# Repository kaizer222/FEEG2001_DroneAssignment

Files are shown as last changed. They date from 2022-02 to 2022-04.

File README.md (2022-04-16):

# FEEG2001_DroneAssignment
GROUP 11 FEEG2001 SEMESTER 2 MULTIROTOR DESIGN PROJECT 

Arduino Code is now tested and working! 

Contribution:
1) SD Card coding	:	James Tang
2) MPU coding		:	Kai Sheng
3) Gimbal coding	:	Kai Wen, Jayce
4) Troubleshooting	:	Kai Wen

To do:
1) Yaw axis stabilisation (optional)

Sources:
1) Gimbal Code	: https://howtomechatronics.com/projects/diy-arduino-gimbal-self-stabilizing-platform/
2) MPU Code	: https://github.com/ElectronicCats/mpu6050/tree/master/examples/MPU6050_DMP6

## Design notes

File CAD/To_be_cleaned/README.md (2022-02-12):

# SolidWorks 3D CAD Files  

## 🚀 Current development  
- Cuboid body with X-configuration arm
- Selection of landing gear
- Selection of material (FEA & Granta Edupack etc.) 

## 🧐 Changelog  
13 Feb 21 — Add files via upload  

## 📃 File extensions  
**`.SLDPRT`** &emsp; SOLIDWORKS Part File  
**`.SLDASM`** &emsp; SOLIDWORKS Assembly File  
**`.STL   `** &emsp;  File type compatible for 3D additive manufacturing  

*I'm using SOLIDWORKS 2020 Student Edition, so if you are using a more recent version it should be backwards compatible.*  

## ⚙ Contents  

### `Assembly1.SLDASM` 
 
<table>
  <tr align="center">
    <th>Component filename</th>
    <th>Description</th>
    <th>Quantity</th>
  </tr>
  <tr align="center">
    <td>arm.SLDPRT</td>
    <td>X-configuration arm</td>
    <td>1</td>
  </tr>
  <tr align="center">
    <td>blade.SLDPRT</td>
    <td>Rotor blade</td>
    <td>4</td>
  </tr>
  <tr align="center">
    <td>body.SLDPRT</td>
    <td>Hexagonal body</td>
    <td>1</td>
  </tr>
  <tr align="center">
    <td>gimbal1.SLDPRT</td>
    <td>Gimbal subpart</td>
    <td>1</td>
  </tr>
    <tr align="center">
    <td>gimbal2.SLDPRT</td>
    <td>Gimbal subpart</td>
    <td>1</td>
  </tr>
    <tr align="center">
    <td>gimbal3.SLDPRT</td>
    <td>Gimbal subpart</td>
    <td>1</td>
  </tr>
    <tr align="center">
    <td>gimbal4.SLDPRT</td>
    <td>Gimbal subpart</td>
    <td>1</td>
  </tr>
    <tr align="center">
    <td>camera.SLDPRT</td>
    <td>Camera</td>
    <td>1</td>
  </tr>
</table>

Associated .STL file: [concept1.STL](https://github.com/kaizer222/FEEG2001_DroneAssignment/blob/main/SolidWorks%20CAD/concept1.STL)  
*The gimbal model used in this assembly is inaccurate and oversimplified, please refer to `ggimbal_assem.SLDASM` instead.*

### `Assembly2.SLDASM` 
 
<table>
  <tr align="center">
    <th>Component filename</th>
    <th>Description</th>
    <th>Quantity</th>
  </tr>
  <tr align="center">
    <td>arm2.SLDPRT</td>
    <td>H-configuration arm</td>
    <td>1</td>
  </tr>
  <tr align="center">
    <td>blade.SLDPRT</td>
    <td>Rotor blade</td>
    <td>4</td>
  </tr>
  <tr align="center">
    <td>body2.SLDPRT</td>
    <td>Cuboid body</td>
    <td>1</td>
  </tr>
  <tr align="center">
    <td>angle_bracket_15x15x10.SLDPRT</td>
    <td>Angle bracket</td>
    <td>2</td>
</table>

Associated .STL file: [concept2.STL](https://github.com/kaizer222/FEEG2001_DroneAssignment/blob/main/SolidWorks%20CAD/concept2.STL)  

### `servo_assem.SLDASM`  

<table>
  <tr align="center">
    <th>Component filename</th>
    <th>Description</th>
    <th>Quantity</th>
  </tr>
  <tr align="center">
    <td>servo_body.SLDPRT</td>
    <td>Servo body</td>
    <td>1</td>
  </tr>
  <tr align="center">
    <td>servo_blade.SLDPRT</td>
    <td>Servo blade</td>
    <td>1</td>
  </tr>
</table>

Associated .STL file: [servo.STL](https://github.com/kaizer222/FEEG2001_DroneAssignment/blob/main/SolidWorks%20CAD/servo.STL)  
*The modelling of the servo itself is not important, but it helps when modelling the servo housing for the gimbal as in `ggimbal_assem.SLDASM`.*  

### `ggimbal_assem.SLDASM`  

<table>
  <tr align="center">
    <th>Component filename</th>
    <th>Description</th>
    <th>Quantity</th>
  </tr>
  <tr align="center">
    <td>servo_body.SLDPRT</td>
    <td>Servo body</td>
    <td>3</td>
  </tr>
  <tr align="center">
    <td>servo_blade.SLDPRT</td>
    <td>Servo blade</td>
    <td>3</td>
  <tr align="center">
    <td>camera_scaled.SLDPRT</td>
    <td>Just a fancier camera 📸</td>
    <td>1</td>
  </tr>
  <tr align="center">
    <td>servo_bolt.SLDPRT</td>
    <td>Servo bolt (short)</td>
    <td>2</td>
  </tr>
  <tr align="center">
    <td>servo_bolt_long.SLDPRT</td>
    <td>Servo bolt (long)</td>
    <td>4</td>
  </tr>
  <tr align="center">
    <td>servo_nut.SLDPRT</td>
    <td>Servo nut</td>
    <td>6</td>
  </tr>
  <tr align="center">
    <td>servo_housing1.SLDPRT</td>
    <td>Servo housing (roll direction)</td>
    <td>1</td>
  </tr>
  <tr align="center">
    <td>servo_housing2.SLDPRT</td>
    <td>Servo housing (pitch direction)</td>
    <td>1</td>
  </tr>
</table>

Associated .STL file: [gimbal.STL](https://github.com/kaizer222/FEEG2001_DroneAssignment/blob/main/SolidWorks%20CAD/gimbal.STL)  
*Three degrees of rotation freedom (DOF-3R), each with π radians.*

---

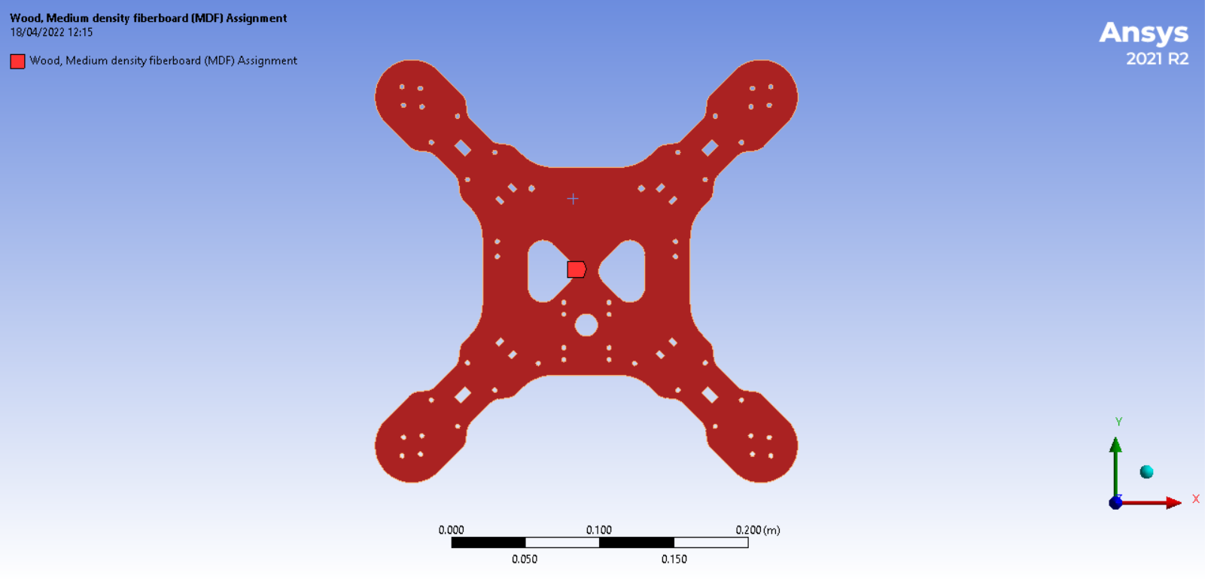
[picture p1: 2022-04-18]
img/Screenshot 2022-04-18 121616.png

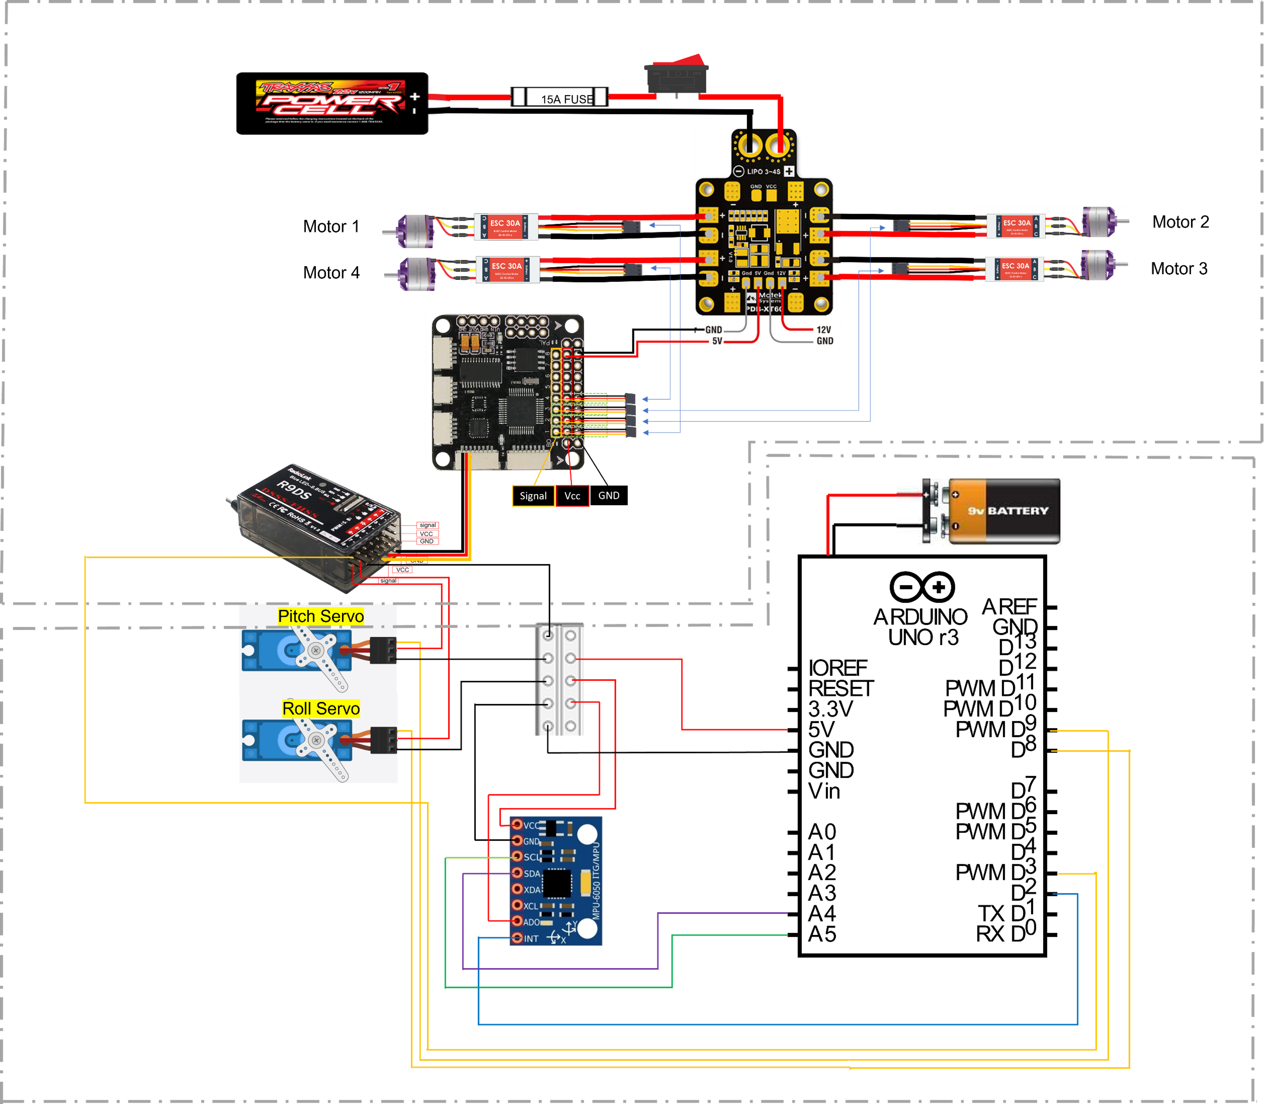
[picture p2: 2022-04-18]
circuit_diagram/pictorial_circuit_diagram.png

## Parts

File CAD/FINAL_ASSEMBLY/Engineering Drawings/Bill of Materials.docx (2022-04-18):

ASSY, Quadcopter Drone — Bill of Materials (BOM)

Prepared by:

Audited by:

REMARKS (for internal use only)

No. | Description | Part Drawing Number | No. Off

Parts
1 | Arm | P1 | 1
2 | SUBASSY, Rib | A1 | 1
3 | Propeller blade | P2 | 4
4 | Motor | P3 | 4
5 | SUBASSY, Landing gear | A2 | 4
6 | Rubber pad | P4 | 4
7 | Arduino and data logging shield | P5 | 1
8 | Li-Po battery | P6 | 1
9 | Servo mount | P7 | 2
10 | Servo housing (roll) | P8 | 1
11 | Servo horn (pitch) | P9 | 1
12 | Camera | P10 | 1
13 | Camera housing | P11 | 1
14 | SG90 micro servo 9g | P12 | 1
15 | Servo horn (roll) | P13 | 1
16 | MG995 servo | P14 | 1
17 | Tray holder | P15 | 2
18 | SUBASSY, Tray | A3 | 1
19 | Receiver/Transmitter | P16 | 1

Fasteners
20 | Angle bracket α (10 mm x 14 mm x 25 mm) | F1 | 16
21 | Angle bracket β (15 mm x 18 mm x 20 mm) | F2 | 4
22 | Bolt (Allen) M3 x 20 mm | F3 | 16
23 | Bolt (Phillips) M2 x 5 mm | F4 | 4
24 | Bolt (Phillips) M2 x 30 mm | F5 | 2
25 | Bolt (Phillips) M3 x 8 mm | F6 | 4
26 | Bolt (Phillips) M3 x 10 mm | F7 | 22
27 | Bolt (Phillips) M3 x 20 mm | F8 | 26
28 | Bolt (Phillips) M4 x 30 mm | F9 | 4
29 | M2 nut | F10 | 2
30 | M3 nut | F11 | 52
31 | M4 nut | F12 | 6
32 | M3 washer | F13 | 36
33 | M4 washer | F14 | 2

Assembly number: A0

Revision: 3

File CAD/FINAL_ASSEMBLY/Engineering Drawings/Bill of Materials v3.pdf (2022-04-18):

## ASSY, Quadcopter Drone — Bill of Materials (BOM)

No. | Description | Part Drawing Number | No. Off

Parts
1 | Arm | P1 | 1
2 | SUBASSY, Rib | A1 | 1
3 | Propeller blade | P2 | 4
4 | Motor | P3 | 4
5 | SUBASSY, Landing gear | A2 | 4
6 | Rubber pad | P4 | 4
7 | Arduino and data logging shield | P5 | 1
8 | Li-Po battery | P6 | 1
9 | Servo mount | P7 | 2
10 | Servo housing (roll) | P8 | 1
11 | Servo horn (pitch) | P9 | 1
12 | Camera | P10 | 1
13 | Camera housing | P11 | 1
14 | SG90 micro servo 9g | P12 | 1
15 | Servo horn (roll) | P13 | 1
16 | MG995 servo | P14 | 1
17 | Tray holder | P15 | 2
18 | SUBASSY, Tray | A3 | 1
19 | Receiver/Transmitter | P16 | 1

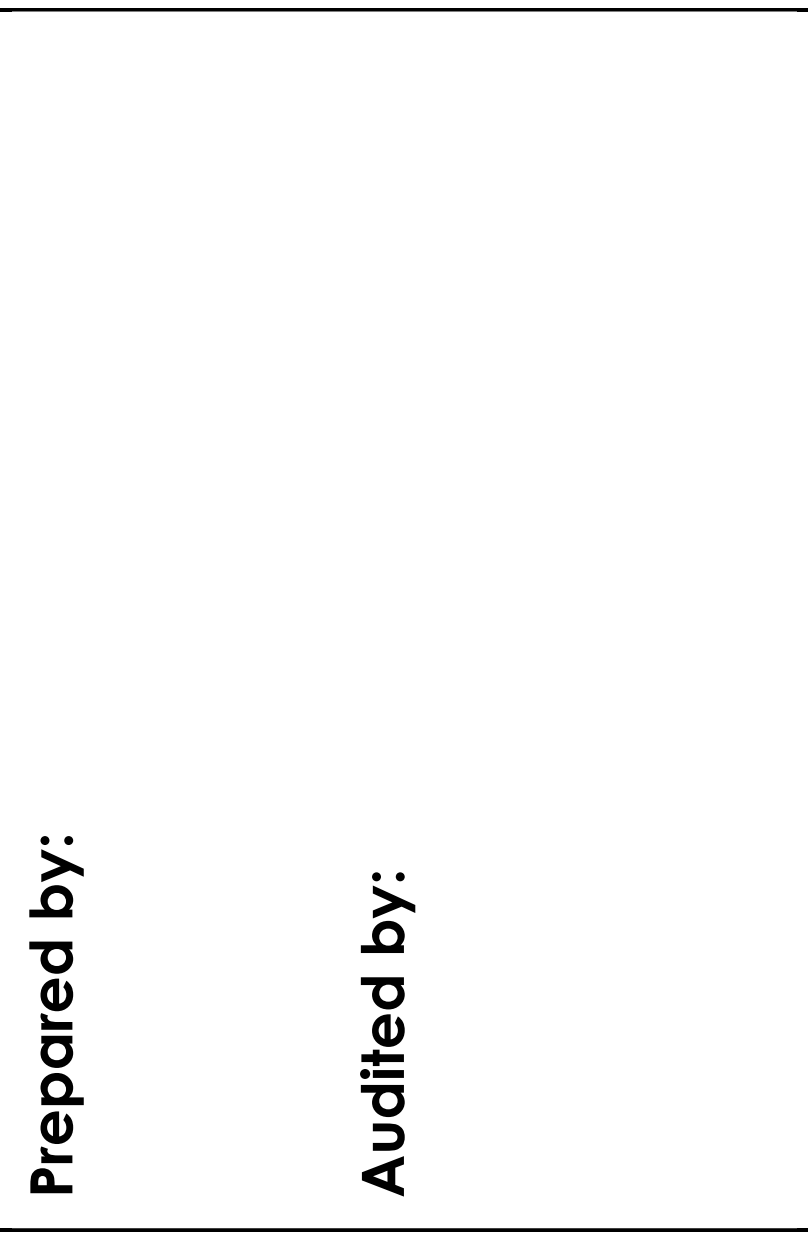
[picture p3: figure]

Fasteners
20 | Angle bracket α (10 mm x 14 mm x 25 mm) | F1 | 16
21 | Angle bracket β (15 mm x 18 mm x 20 mm) | F2 | 4
22 | Bolt (Allen) M3 x 20 mm | F3 | 16
23 | Bolt (Phillips) M2 x 5 mm | F4 | 4
24 | Bolt (Phillips) M2 x 30 mm | F5 | 2
25 | Bolt (Phillips) M3 x 8 mm | F6 | 4
26 | Bolt (Phillips) M3 x 10 mm | F7 | 22
27 | Bolt (Phillips) M3 x 20 mm | F8 | 26
28 | Bolt (Phillips) M4 x 30 mm | F9 | 4
29 | M2 nut | F10 | 2
30 | M3 nut | F11 | 52
31 | M4 nut | F12 | 6
32 | M3 washer | F13 | 36

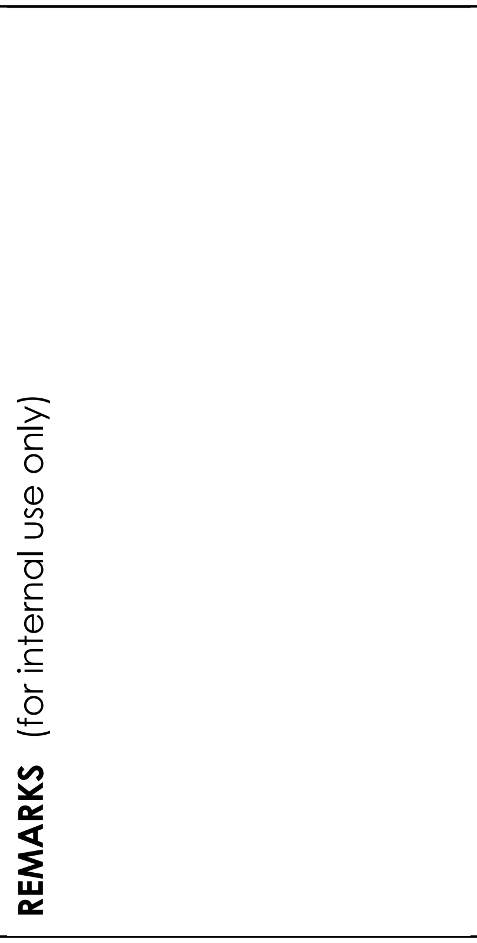
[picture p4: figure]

33 | M4 washer | F14 | 2 | REMARKS ⁽for internal use only⁾ Prepared by: | Audited by: Assembly number: A0

Revision: 3

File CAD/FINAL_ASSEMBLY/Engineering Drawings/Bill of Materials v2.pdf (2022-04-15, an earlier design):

## ASSY, Quadcopter Drone — Bill of Materials (BOM)

No. | Description | Part Drawing Number | No. Off

Parts
1 | Arm | P1 | 1
2 | SUBASSY, Rib | A1 | 1
3 | Propeller blade | P2 | 4
4 | Motor | P3 | 4
5 | SUBASSY, Landing gear | A2 | 4
6 | Rubber pad | P4 | 4
7 | Arduino and data logging shield | P5 | 1
8 | Li-Po battery | P6 | 1
9 | Servo mount | P7 | 2
10 | MG995 servo | P8 | 1
11 | SG90 micro servo 9g | P9 | 2
12 | Servo housing (roll) | P10 | 1
13 | Servo horn (yaw) | P11 | 1
14 | Servo housing (yaw) | P12 | 1
15 | Servo horn (pitch) | P13 | 1
16 | Camera housing | P14 | 1
17 | Camera | P15 | 1
18 | Servo horn (roll) | P16 | 1
19 | Tray holder | P17 | 2
20 | SUBASSY, Tray | A3 | 1
21 | Receiver/Transmitter | P18 | 1


Fasteners
22 | Angle bracket α (10 mm x 14 mm x 25 mm) | F1 | 16
23 | Angle bracket β (15 mm x 18 mm x 20 mm) | F2 | 4
24 | Bolt (Allen) M3 x 20 mm | F3 | 16
25 | Bolt (Phillips) M2 x 5 mm | F4 | 4
26 | Bolt (Phillips) M2 x 30 mm | F5 | 2
27 | Bolt (Phillips) M3 x 5 mm | F6 | 1
28 | Bolt (Phillips) M3 x 8 mm | F7 | 4
29 | Bolt (Phillips) M3 x 10 mm | F8 | 24
30 | Bolt (Phillips) M3 x 20 mm | F9 | 26
31 | Bolt (Phillips) M4 x 30 mm | F10 | 6
32 | M2 nut | F11 | 4
33 | M3 nut | F12 | 52
34 | M4 nut | F13 | 6
35 | M3 washer | F14 | 40


36 | M4 washer | F15 | 2 | REMARKS ⁽for internal use only⁾ Prepared by: | Audited by:

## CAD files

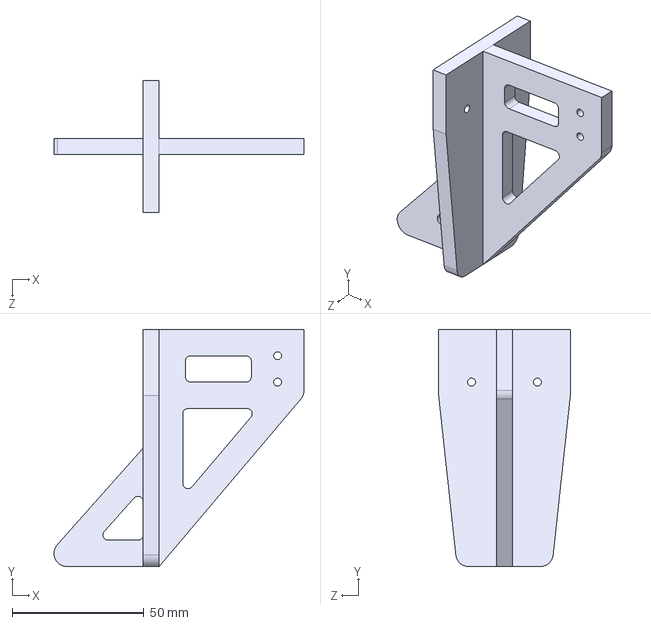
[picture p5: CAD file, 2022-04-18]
CAD/FINAL_ASSEMBLY/FEA/IGS files/SUBASSY_landinggear.IGS
94.9 x 90.0 x 50.0 mm

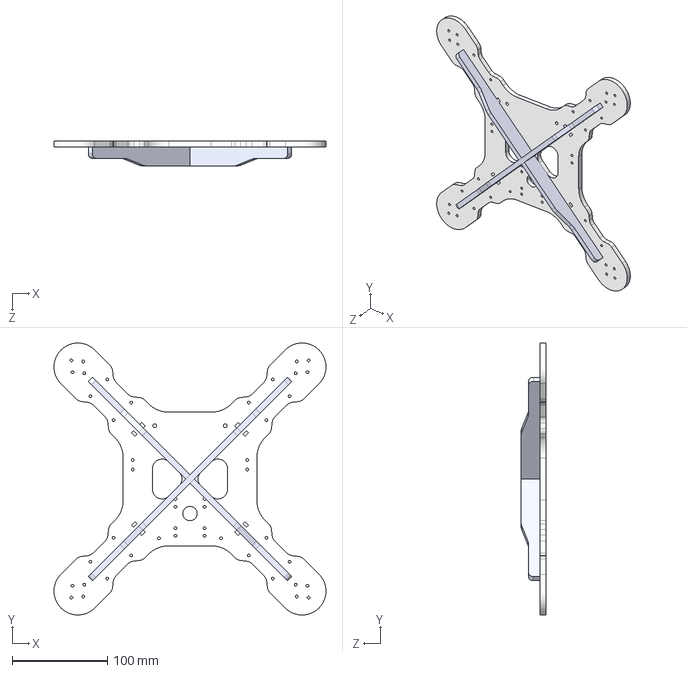
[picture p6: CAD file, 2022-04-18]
CAD/FINAL_ASSEMBLY/FEA/IGS files/SUBASSY_body_lid5_with_ribs.IGS
285.0 x 285.0 x 26.0 mm

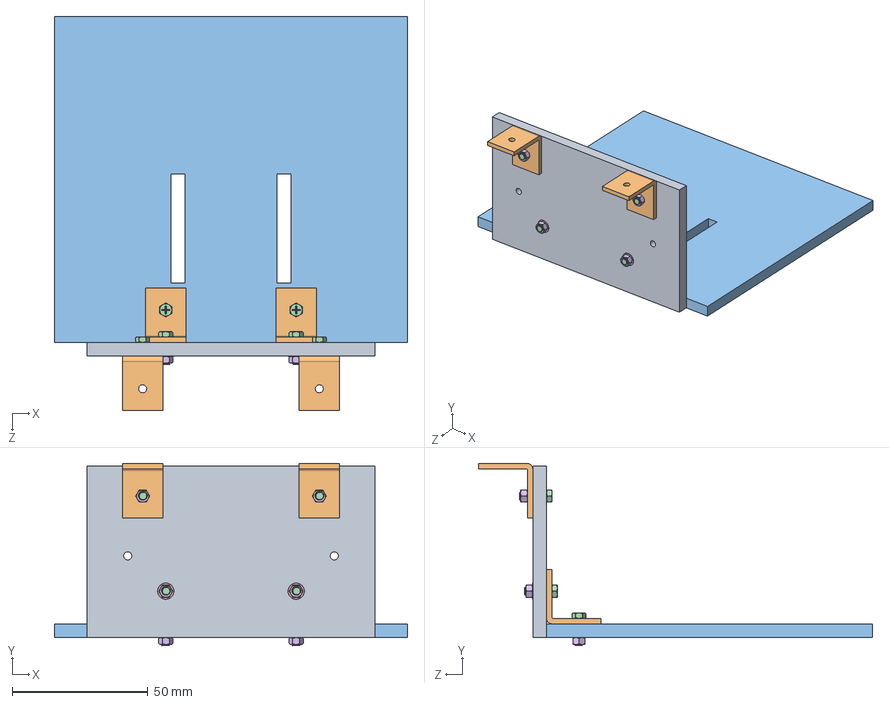
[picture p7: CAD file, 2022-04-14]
CAD/FINAL_ASSEMBLY/SUBASSY_tray.SLDASM
130.0 x 67.0 x 145.0 mm
tray_vertical
L_bracket_beta x 4
tray_horizontal
bolt_phillips_M3_10mm x 6
washer_M3 x 6
nut_M3 x 6

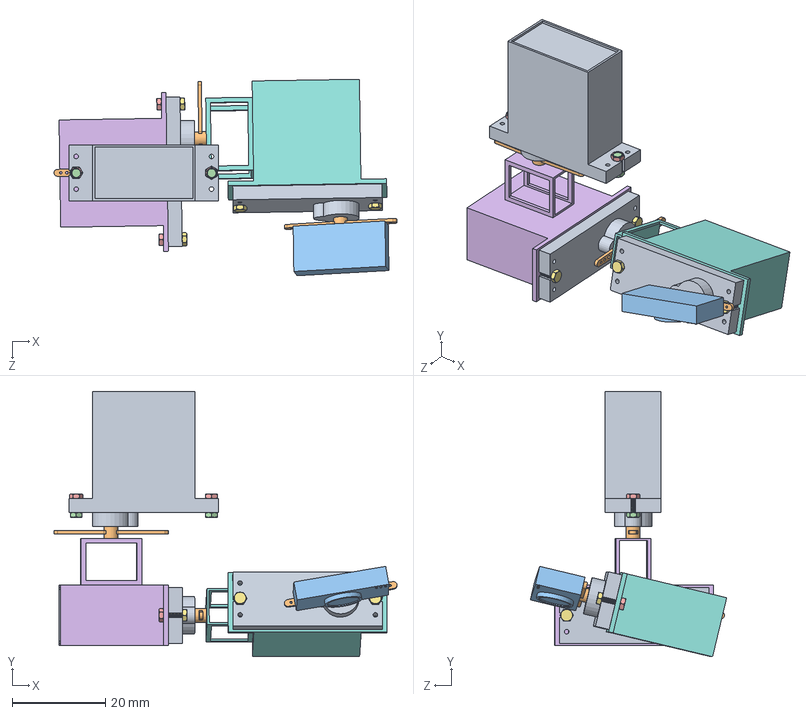
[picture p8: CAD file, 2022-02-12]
CAD/To_be_cleaned/ggimbal_assem.SLDASM
73.5 x 56.9 x 42.1 mm
servo_body x 3
servo_blade x 3
camera_scaled
servo_bolt x 2
servo_nut x 6
servo_housing1
servo_bolt_long x 4
servo_housing2

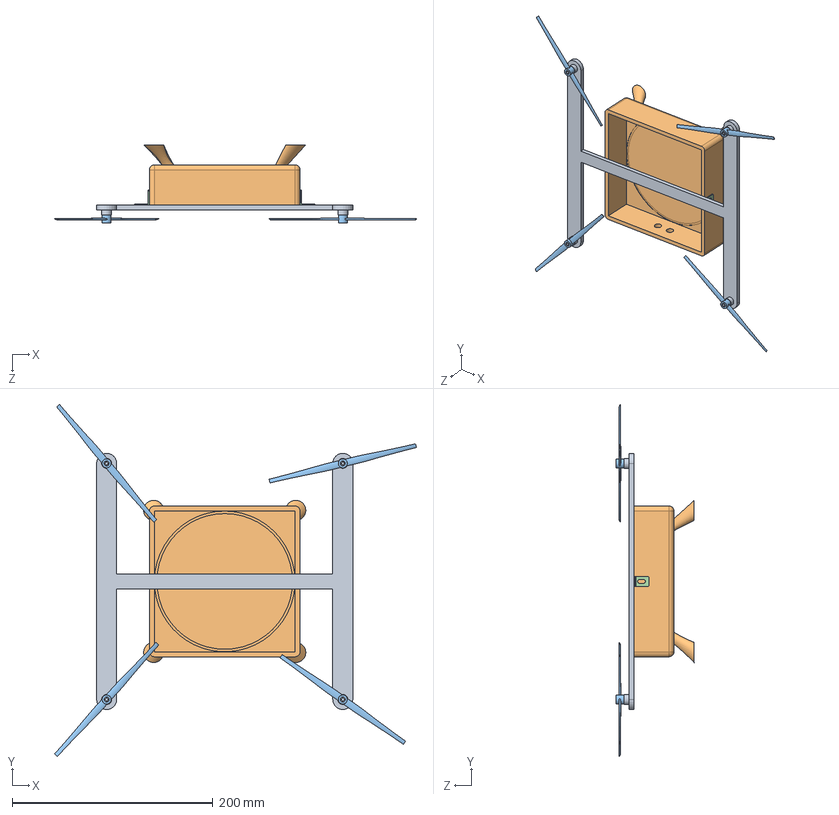
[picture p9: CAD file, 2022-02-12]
CAD/To_be_cleaned/Assembly2.SLDASM
360.2 x 350.4 x 78.0 mm
arm2
blade x 4
angle_bracket_15x15x10 x 2

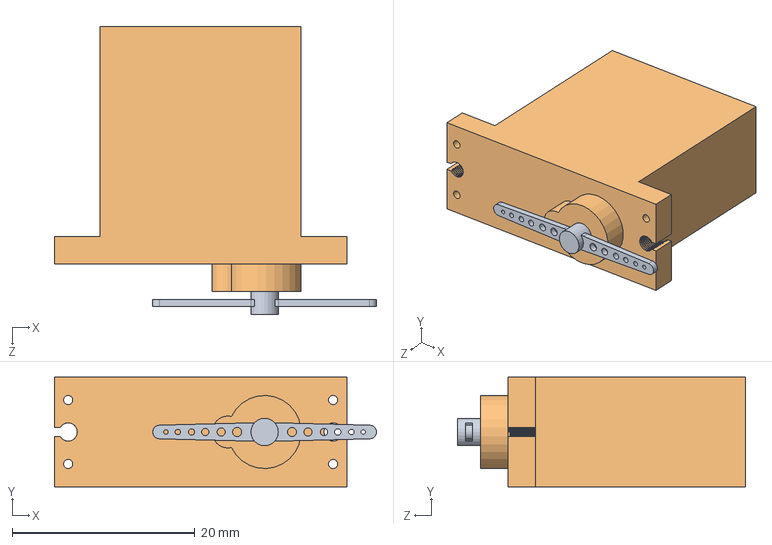
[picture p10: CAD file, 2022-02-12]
CAD/To_be_cleaned/servo_assem.SLDASM
35.2 x 12.0 x 31.5 mm
servo_blade
servo_body

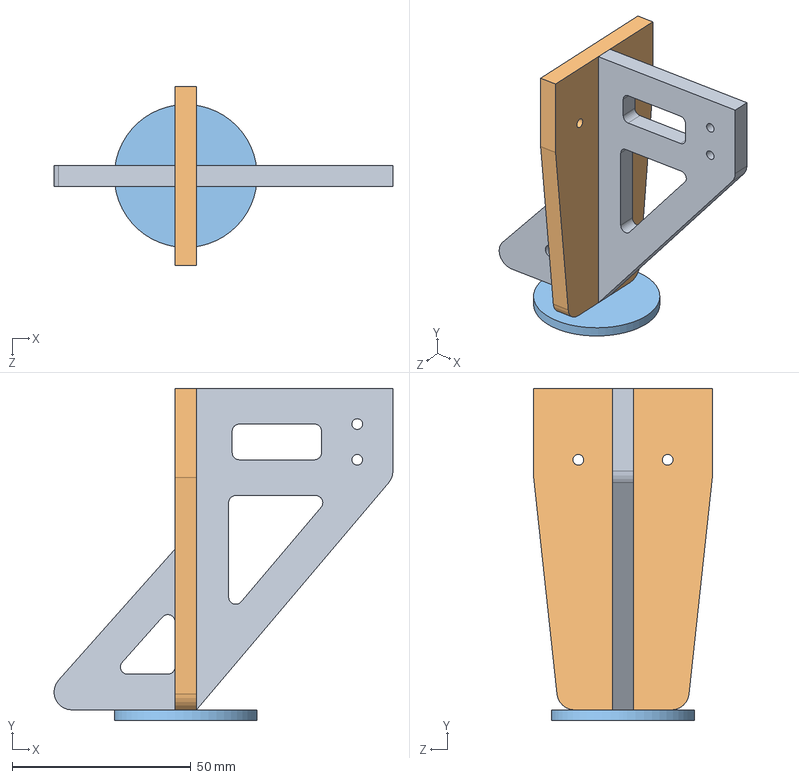
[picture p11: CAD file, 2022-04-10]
CAD/FINAL_ASSEMBLY/SUBASSY_landinggear.SLDASM
94.9 x 93.0 x 50.0 mm
LDG_GEAR_E_mal_2
LDG_GEAR_E_FEM_2
landinggear_pad

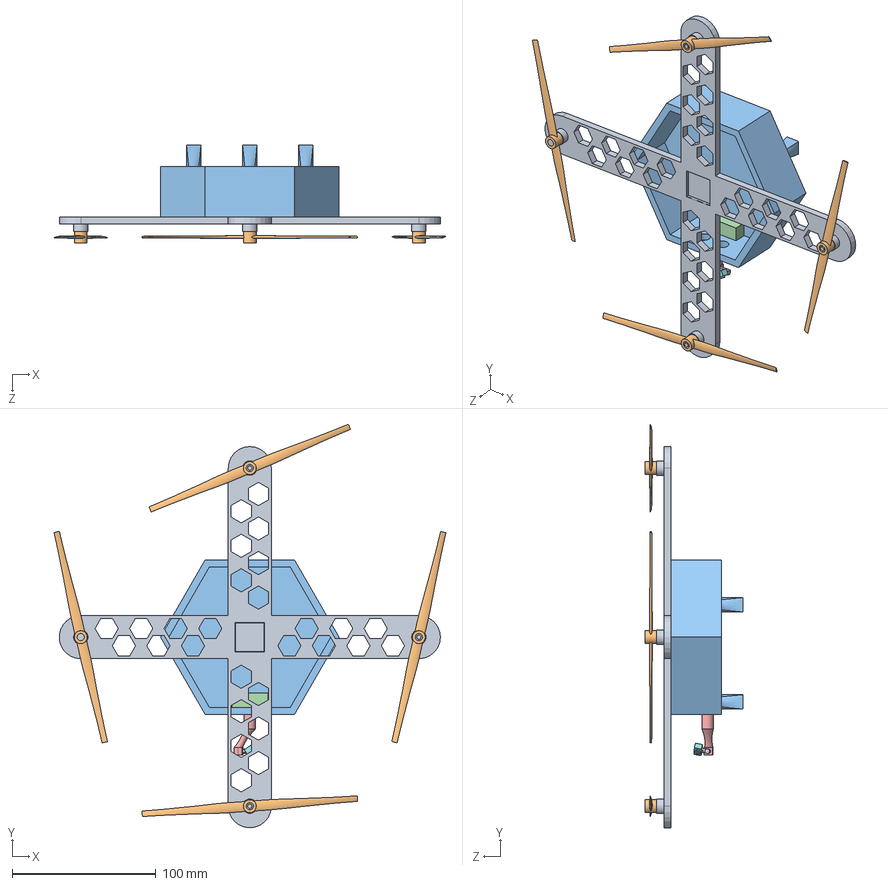
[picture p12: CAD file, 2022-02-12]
CAD/To_be_cleaned/Assembly1.SLDASM
272.5 x 280.5 x 68.0 mm
arm
blade x 4
gimbal1
gimbal2
gimbal3
gimbal4
camera

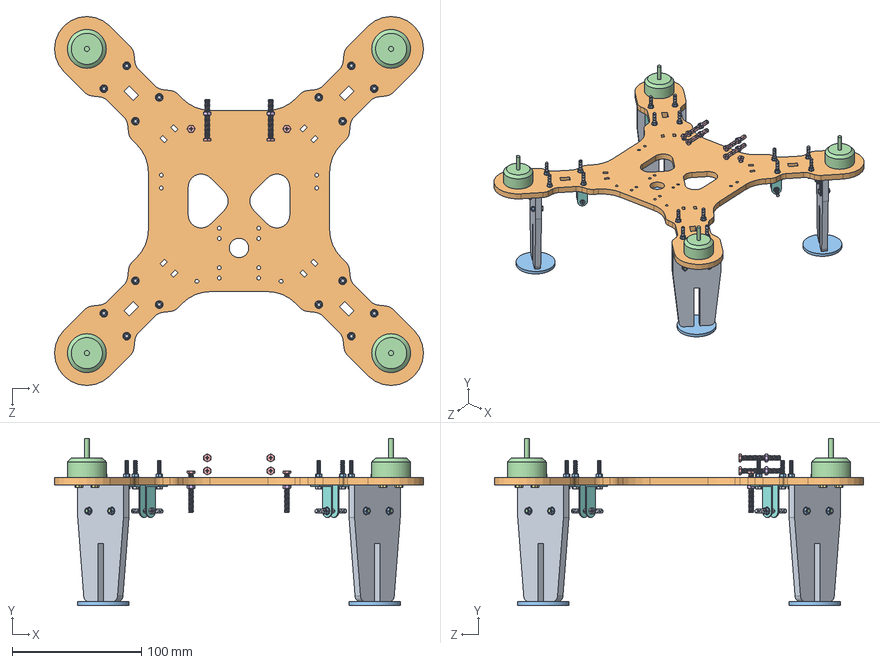
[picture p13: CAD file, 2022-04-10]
CAD/FINAL_ASSEMBLY/ASSY.SLDASM
285.0 x 129.0 x 285.0 mm
body_lid5
LDG_GEAR_E_FEM_2 x 4
landinggear_pad x 4
motor x 4
bolt_phillips_M4_30mm x 6
nut_M4 x 6
bolt_allen_M3_20mm x 16
L_bracket x 16
bolt_phillips_M3_20mm x 20
washer_M3 x 28
nut_M3 x 28
bolt_phillips_M3_10mm x 8
washer_M4 x 2

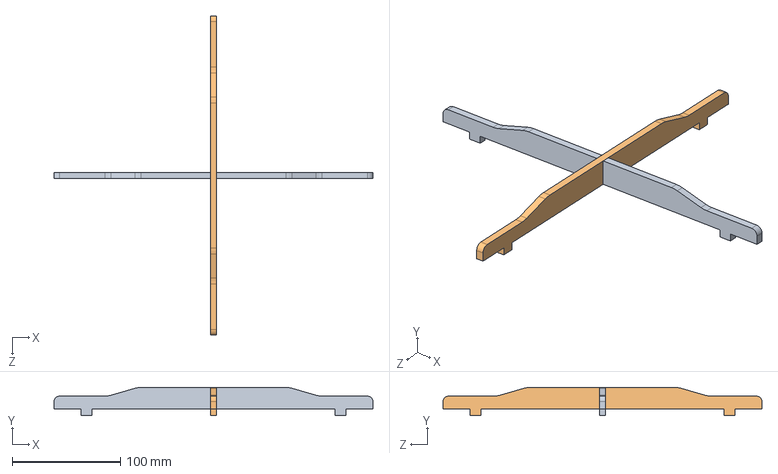
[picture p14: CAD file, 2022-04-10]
CAD/FINAL_ASSEMBLY/SUBASSY_rib.SLDASM
295.3 x 26.0 x 295.3 mm
lid_rib_bot
lid_rib_top

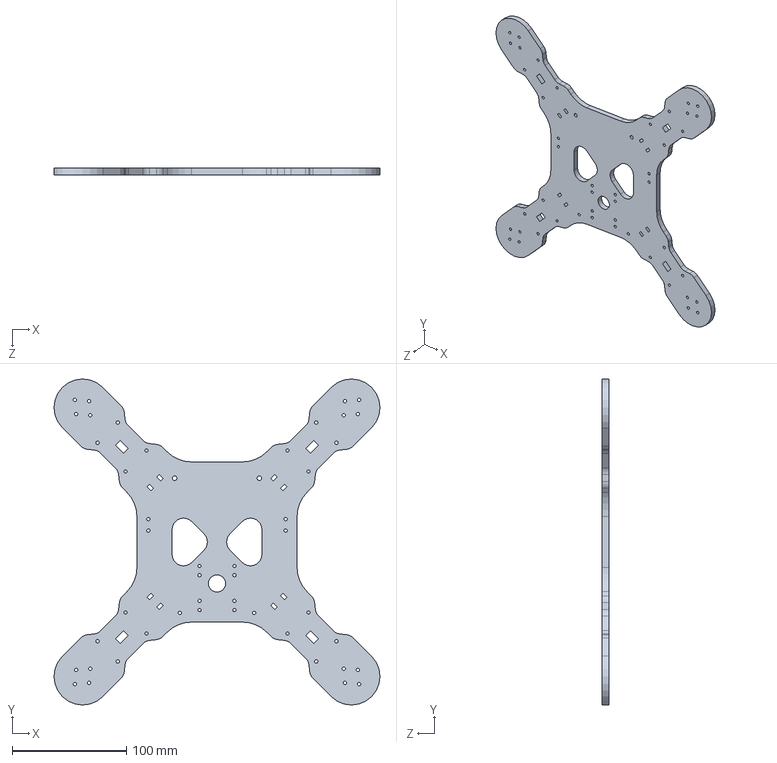
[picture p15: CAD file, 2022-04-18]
CAD/FINAL_ASSEMBLY/body_lid5.SLDPRT
285.0 x 285.0 x 6.00 mm

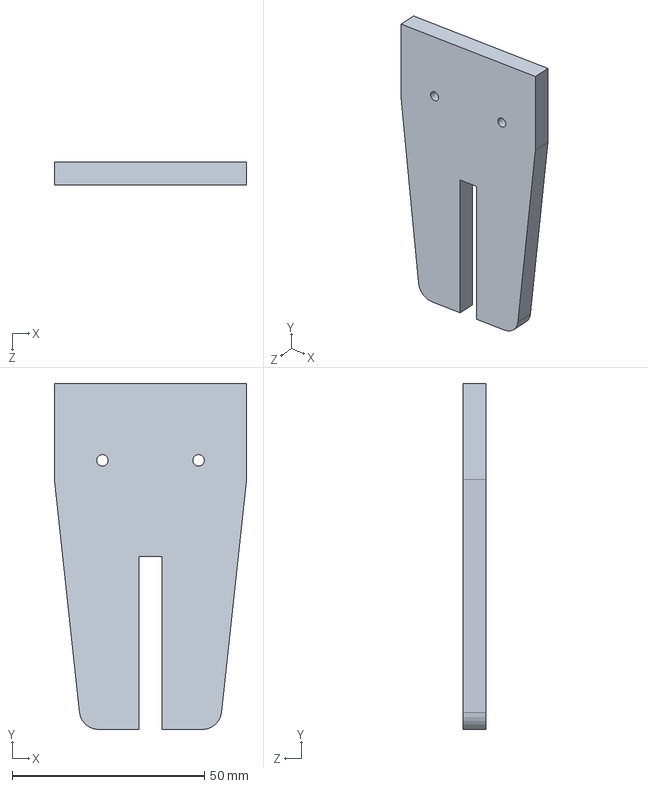
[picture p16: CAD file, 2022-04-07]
CAD/landing_gear/LDG_GEAR_E_FEM_2.SLDPRT
50.0 x 90.0 x 6.00 mm

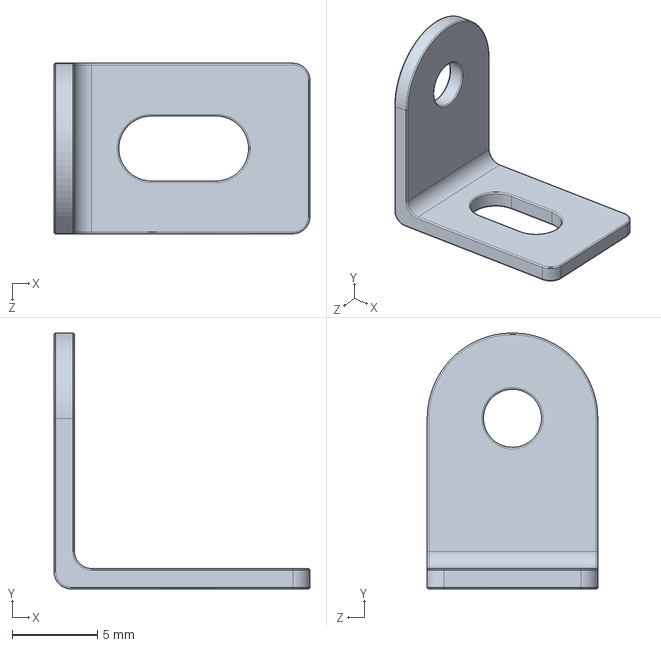
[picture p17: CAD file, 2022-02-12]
CAD/To_be_cleaned/angle_bracket_15x15x10.SLDPRT
15.0 x 15.0 x 10.0 mm

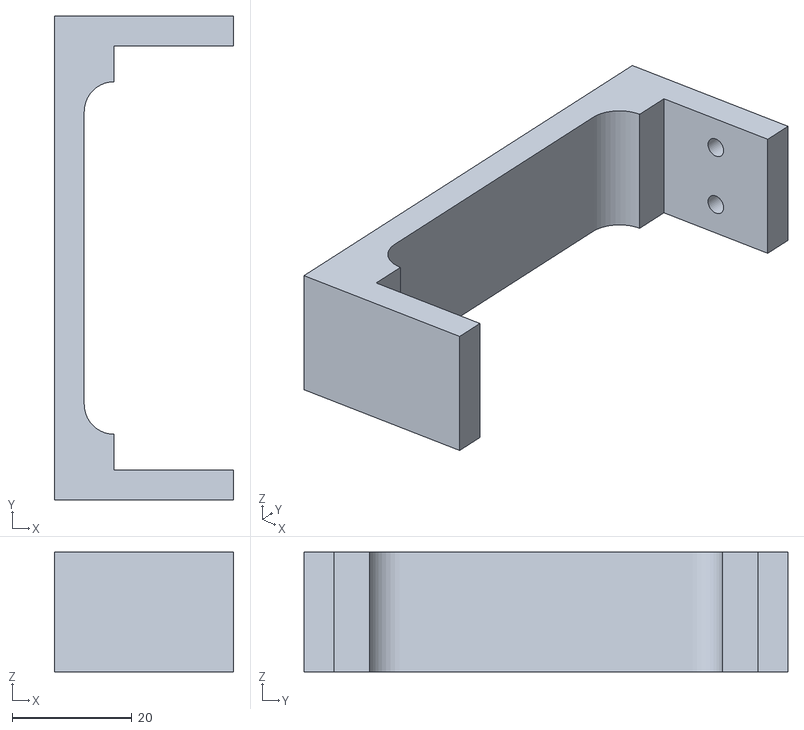
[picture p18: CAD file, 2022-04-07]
CAD/tray_holder/Tray_Holder-3D print-2 pcs.STL
30.0 x 81.0 x 20.0

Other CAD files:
CAD/X_arm/x_arm_5.SLDPRT
CAD/X_arm_supports/LIDRIBTOP_MDF_2PCS.DXF
CAD/FINAL_ASSEMBLY/FEA/IGS files/body_lid5_fea.IGS
CAD/FINAL_ASSEMBLY/tx_rx.SLDPRT
CAD/FINAL_ASSEMBLY/Engineering Drawings/SUBASSY_landinggear.SLDDRW
CAD/FINAL_ASSEMBLY/Engineering Drawings/SUBASSY_tray.SLDDRW
CAD/FINAL_ASSEMBLY/Engineering Drawings/body_lid5.SLDDRW
CAD/FINAL_ASSEMBLY/Fasteners/L_bracket_alpha.SLDPRT
CAD/FINAL_ASSEMBLY/Fasteners/L_bracket_beta.SLDPRT
CAD/FINAL_ASSEMBLY/Fasteners/bolt_allen_M3_20mm.SLDPRT
CAD/FINAL_ASSEMBLY/Fasteners/bolt_phillips_M2_30mm.SLDPRT
CAD/FINAL_ASSEMBLY/Fasteners/bolt_phillips_M2_5mm.SLDPRT
CAD/FINAL_ASSEMBLY/Fasteners/bolt_phillips_M3_10mm.SLDPRT
CAD/FINAL_ASSEMBLY/Fasteners/bolt_phillips_M3_20mm.SLDPRT
CAD/FINAL_ASSEMBLY/Fasteners/bolt_phillips_M3_5mm.SLDPRT
CAD/FINAL_ASSEMBLY/Fasteners/bolt_phillips_M3_8mm.SLDPRT
CAD/FINAL_ASSEMBLY/Fasteners/bolt_phillips_M4_20mm.SLDPRT
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

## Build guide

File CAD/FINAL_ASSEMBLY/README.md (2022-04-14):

# ✈ Final Assembly  

CAD models and drawings for the final report appendix section. SolidWorks **2021-22** Student Edition.  

**Note: Please save/clone the folder in the root C:/ directory otherwise the assembly file might be corrupt**  
✔ 255 components in total.  

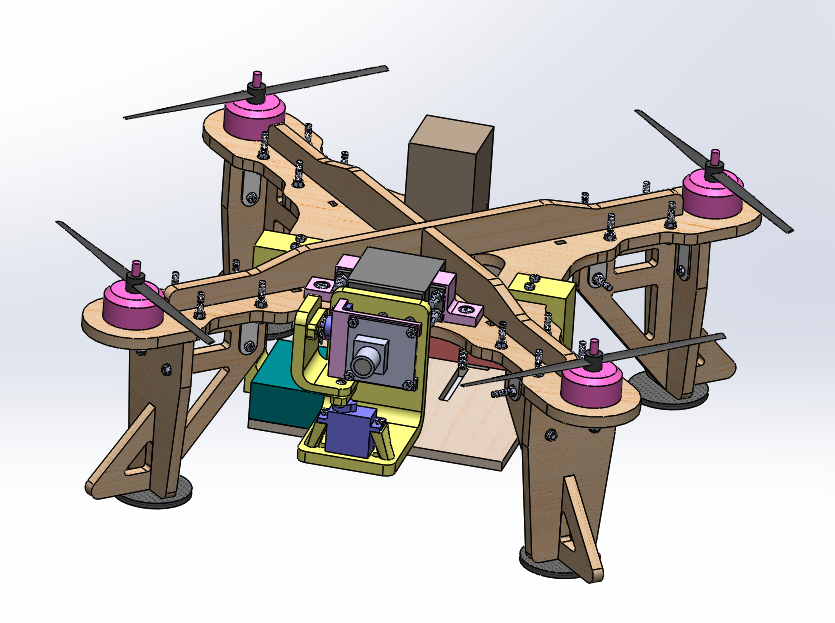
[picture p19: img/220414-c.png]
  
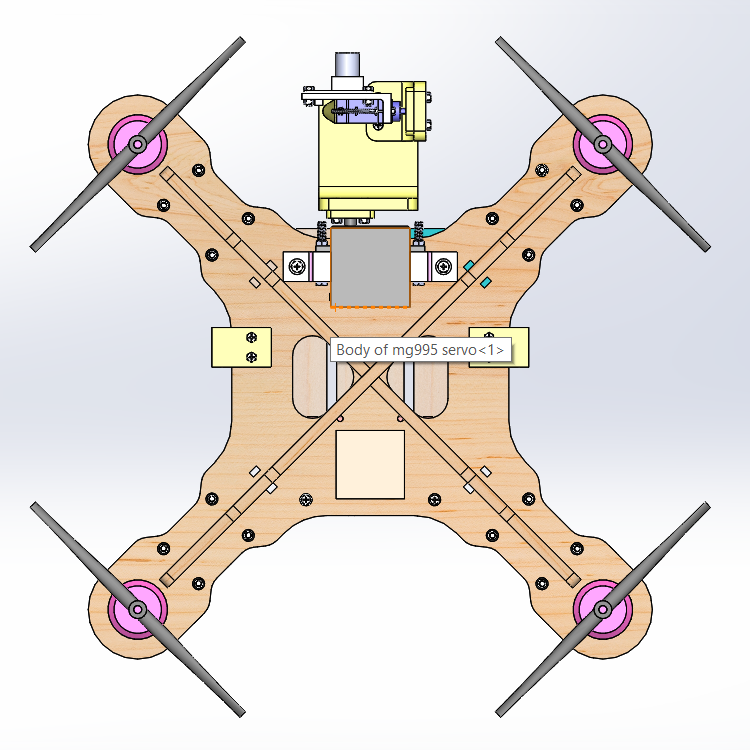
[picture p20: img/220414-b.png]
  
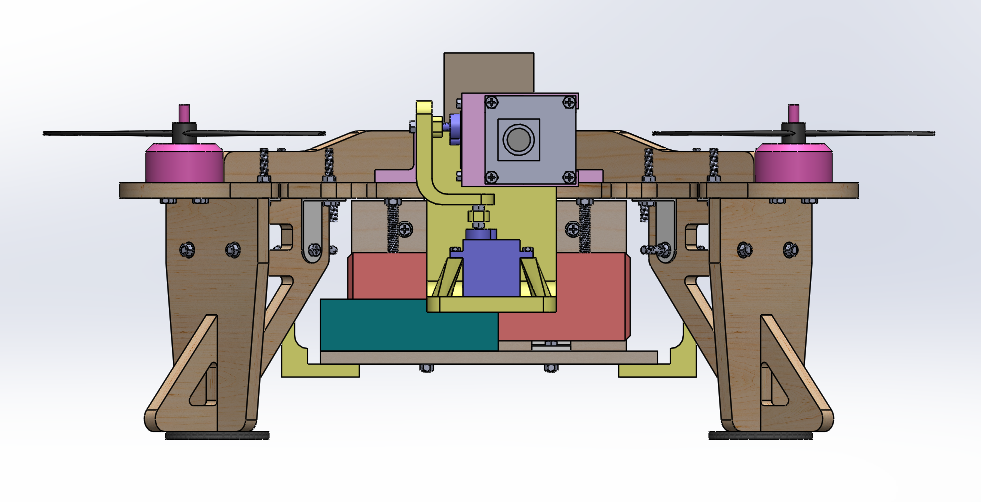
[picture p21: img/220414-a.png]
  
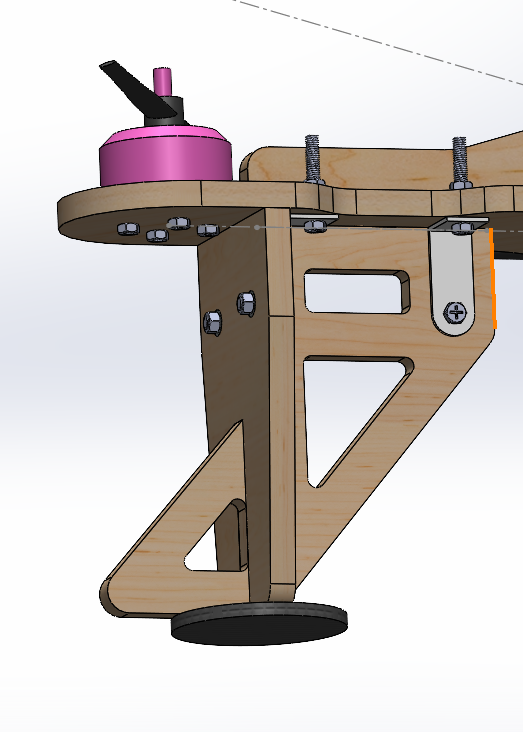
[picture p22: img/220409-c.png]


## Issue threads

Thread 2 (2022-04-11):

src/main FIFO (first-in-first-out) overflow

yonghuatang, 2022-04-11:
Omitting the delay() function might help.

kaizer222, 2022-04-12:
FIFO Overload solved by commenting the set I2C clock speed:

`
// ========================         MPU Setup           ========================//
pinMode (DMP_PIN,OUTPUT);
digitalWrite(DMP_PIN,LOW);
// join I2C bus
  #if I2CDEV_IMPLEMENTATION == I2CDEV_ARDUINO_WIRE
    Wire.begin();
    //Wire.setClock(40000);                //uncommented due to stability issues
  `

Closed 2022-04-12.

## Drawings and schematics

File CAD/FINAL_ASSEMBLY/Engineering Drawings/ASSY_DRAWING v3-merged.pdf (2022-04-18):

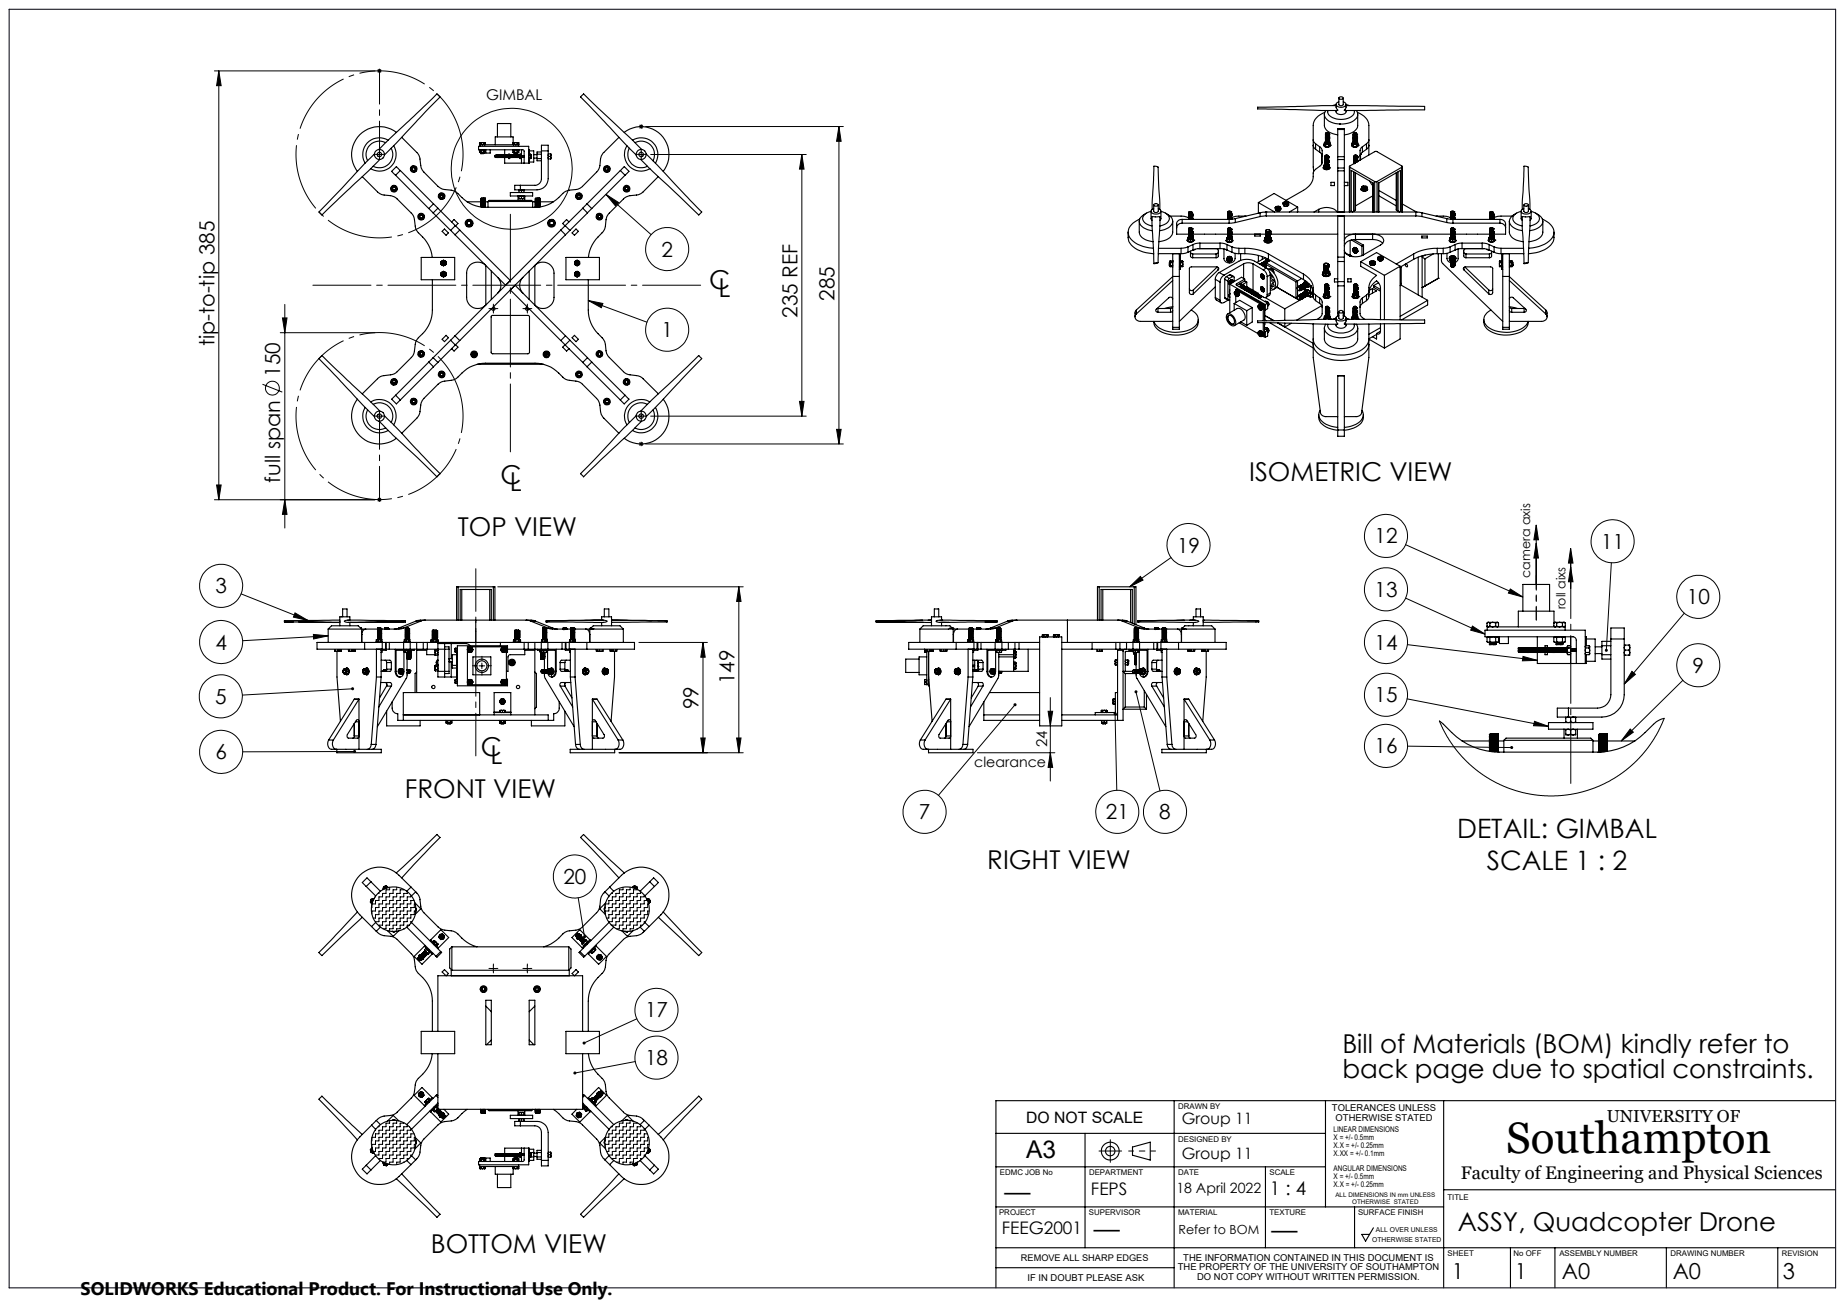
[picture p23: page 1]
235 REF; full span 150; TOP VIEW; FRONT VIEW; RIGHT VIEW; ISOMETRIC VIEW; DETAIL: GIMBAL SCALE 1 : 2; FEPS; 18 April 2022; Group 11; BOTTOM VIEW; camera axis; roll aixs; SHEET; No OFF; ASSEMBLY NUMBER; DRAWING NUMBER; REVISION; PROJECT; SUPERVISOR; MATERIAL; TEXTURE; SURFACE FINISH; TOLERANCES UNLESS OTHERWISE STATED; DRAWN BY; DESIGNED BY; EDMC JOB No; DEPARTMENT; DATE; SCALE; DO NOT SCALE; LINEAR DIMENSIONS X = +/- 0.5mm X.X = +/- 0.25mm X.XX = +/- 0.1mm ANGULAR DIMENSIONS X = +/- 0.5mm

tip-to-tip 385

Bill of Materials (BOM) kindly refer to
back page due to spatial constraints.

Southampton UNIVERSITY OF

Faculty of Engineering and Physical Sciences
ASSY, Quadcopter Drone

ALL DIMENSIONS IN mm UNLESS
OTHERWISE STATED

Refer to BOM

ALL OVER UNLESS

REMOVE ALL SHARP EDGES
IF IN DOUBT PLEASE ASK

THE INFORMATION CONTAINED IN THIS DOCUMENT IS
THE PROPERTY OF THE UNIVERSITY OF SOUTHAMPTON
DO NOT COPY WITHOUT WRITTEN PERMISSION.

SOLIDWORKS Educational Product. For Instructional Use Only.

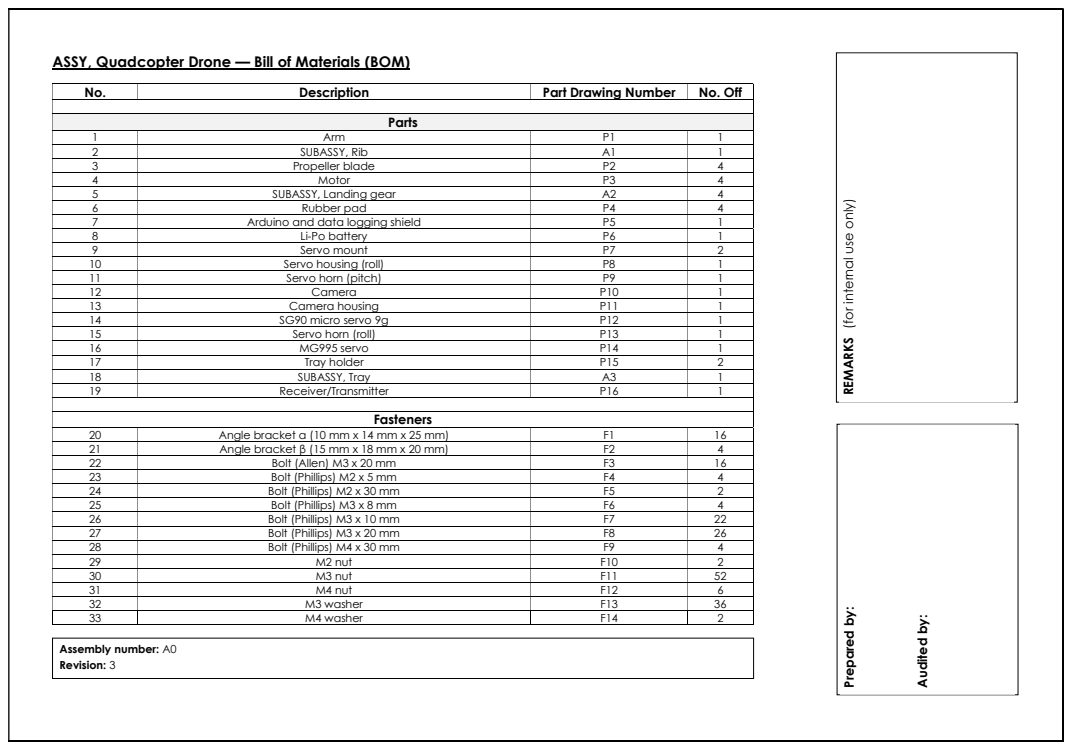
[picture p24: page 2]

ASSY, Quadcopter Drone — Bill of Materials (BOM)

1 | Arm | P1 | 1
2 | SUBASSY, Rib | A1 | 1
3 | Propeller blade | P2 | 4
4 | Motor | P3 | 4
5 | SUBASSY, Landing gear | A2 | 4
6 | Rubber pad | P4 | 4
7 | Arduino and data logging shield | P5 | 1
8 | Li-Po battery | P6 | 1
9 | Servo mount | P7 | 2
10 | Servo housing (roll) | P8 | 1
11 | Servo horn (pitch) | P9 | 1
12 | Camera | P10 | 1
13 | Camera housing | P11 | 1
14 | SG90 micro servo 9g | P12 | 1
15 | Servo horn (roll) | P13 | 1
16 | MG995 servo | P14 | 1
17 | Tray holder | P15 | 2
18 | SUBASSY, Tray | A3 | 1
19 | Receiver/Transmitter | P16 | 1

20 | Angle bracket α (10 mm x 14 mm x 25 mm) | F1 | 16
21 | Angle bracket β (15 mm x 18 mm x 20 mm) | F2 | 4
22 | Bolt (Allen) M3 x 20 mm | F3 | 16
23 | Bolt (Phillips) M2 x 5 mm | F4 | 4
24 | Bolt (Phillips) M2 x 30 mm | F5 | 2
25 | Bolt (Phillips) M3 x 8 mm | F6 | 4
26 | Bolt (Phillips) M3 x 10 mm | F7 | 22
27 | Bolt (Phillips) M3 x 20 mm | F8 | 26
28 | Bolt (Phillips) M4 x 30 mm | F9 | 4
29 | M2 nut | F10 | 2
30 | M3 nut | F11 | 52
31 | M4 nut | F12 | 6
32 | M3 washer | F13 | 36

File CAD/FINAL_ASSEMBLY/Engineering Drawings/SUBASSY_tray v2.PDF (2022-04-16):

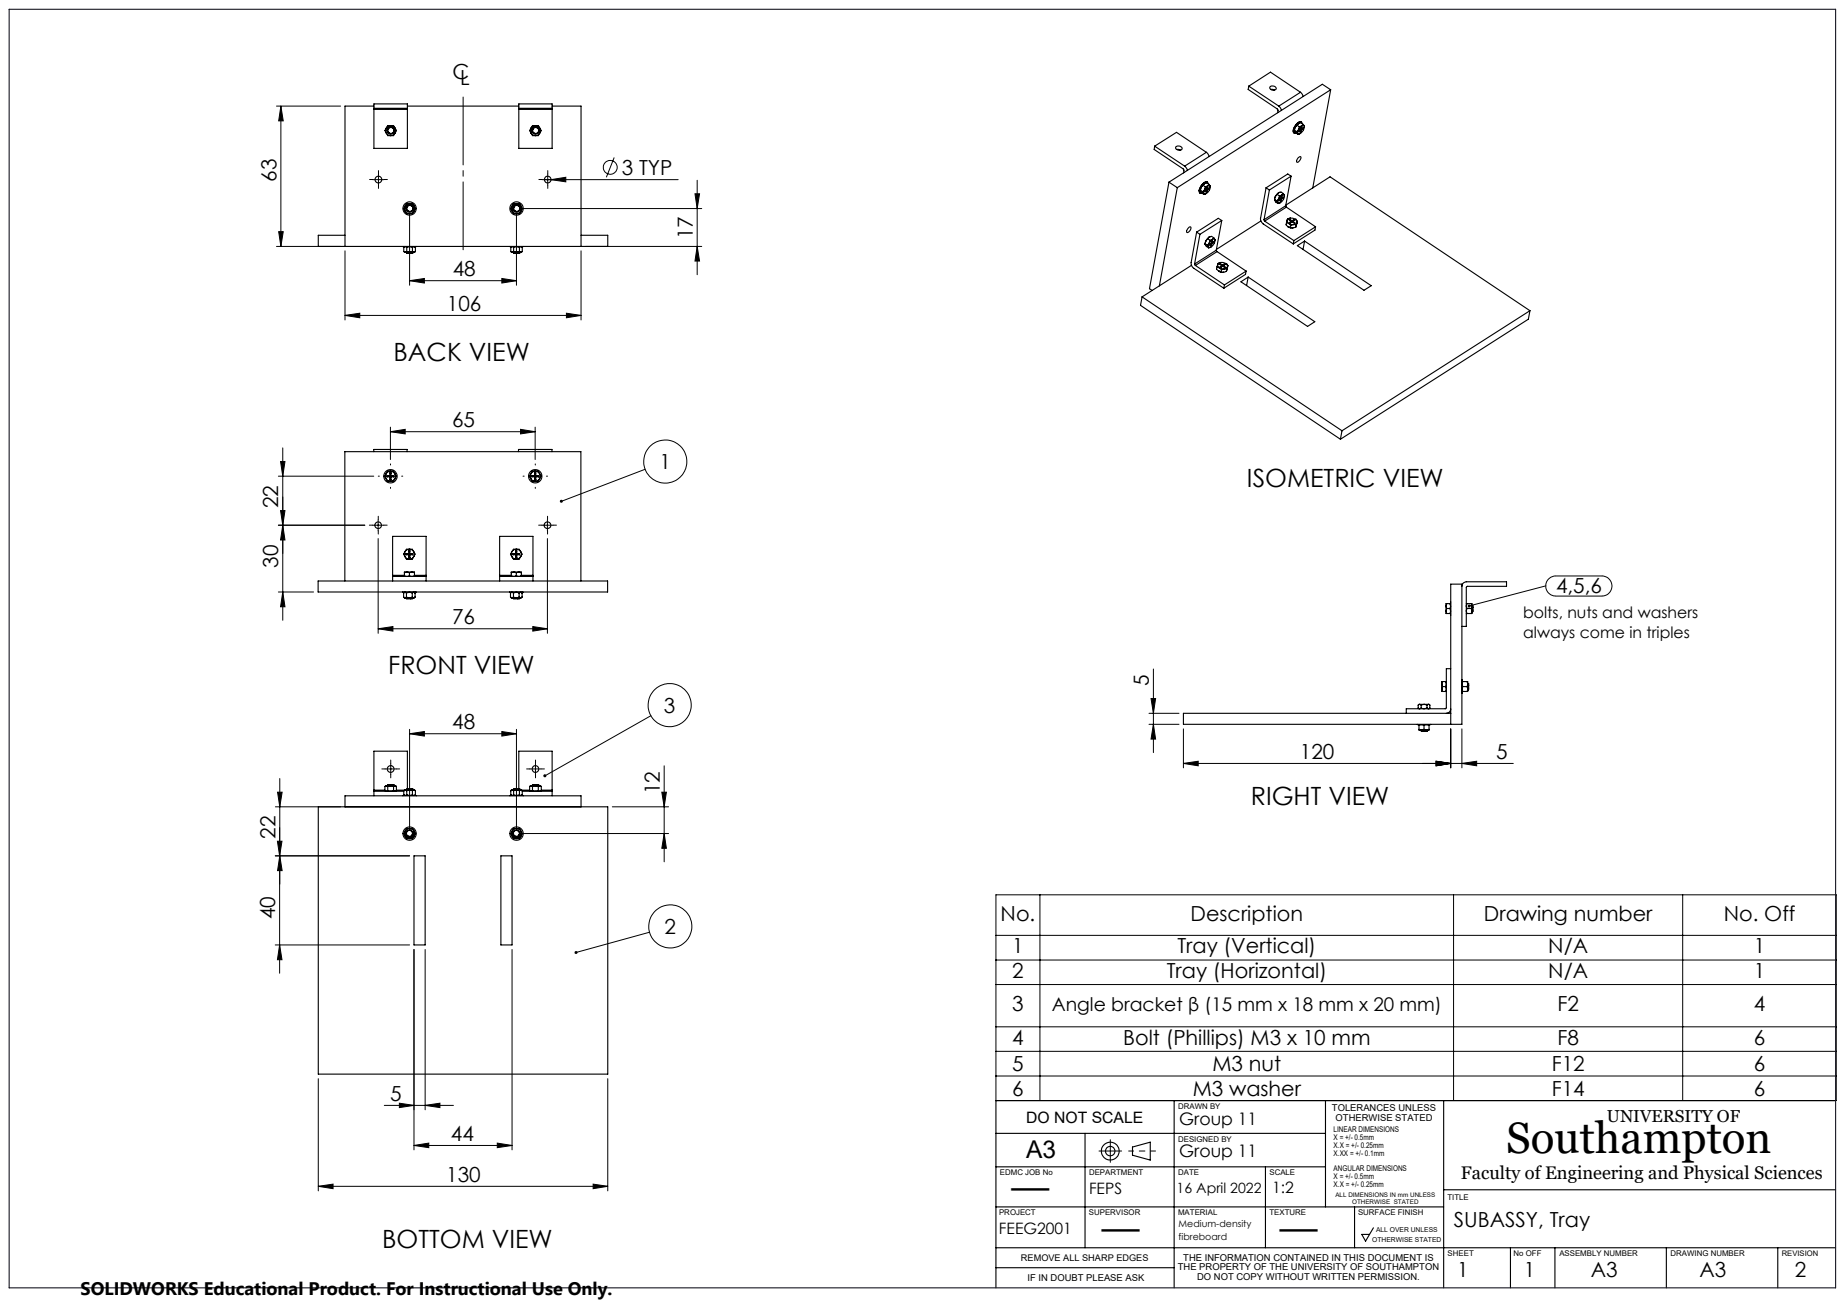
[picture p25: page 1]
3 TYP; ISOMETRIC VIEW 5; Group 11 Group 11; 16 April 2022; SUBASSY, Tray; BACK VIEW; BOTTOM VIEW; FRONT VIEW; RIGHT VIEW; SHEET; No OFF; ASSEMBLY NUMBER; DRAWING NUMBER; REVISION; PROJECT; SUPERVISOR; MATERIAL; TEXTURE; SURFACE FINISH; TOLERANCES UNLESS OTHERWISE STATED; DRAWN BY; DESIGNED BY; EDMC JOB No; DEPARTMENT; DATE; SCALE; DO NOT SCALE; LINEAR DIMENSIONS X = +/- 0.5mm X.X = +/- 0.25mm X.XX = +/- 0.1mm ANGULAR DIMENSIONS X = +/- 0.5mm

bolts, nuts and washers
always come in triples

No. | Description | Drawing number | No. Off
1 | Tray (Vertical) | N/A | 1
2 | Tray (Horizontal) | N/A | 1
3 | Angle bracket β (15 mm x 18 mm x 20 mm) | F2 | 4
4 | Bolt (Phillips) M3 x 10 mm | F8 | 6
5 | M3 nut | F12 | 6
6 | M3 washer | F14 | 6

Southampton UNIVERSITY OF

Faculty of Engineering and Physical Sciences

ALL DIMENSIONS IN mm UNLESS
OTHERWISE STATED

Medium-density
fibreboard
THE INFORMATION CONTAINED IN THIS DOCUMENT IS
THE PROPERTY OF THE UNIVERSITY OF SOUTHAMPTON
DO NOT COPY WITHOUT WRITTEN PERMISSION.

ALL OVER UNLESS

REMOVE ALL SHARP EDGES
IF IN DOUBT PLEASE ASK

SOLIDWORKS Educational Product. For Instructional Use Only.

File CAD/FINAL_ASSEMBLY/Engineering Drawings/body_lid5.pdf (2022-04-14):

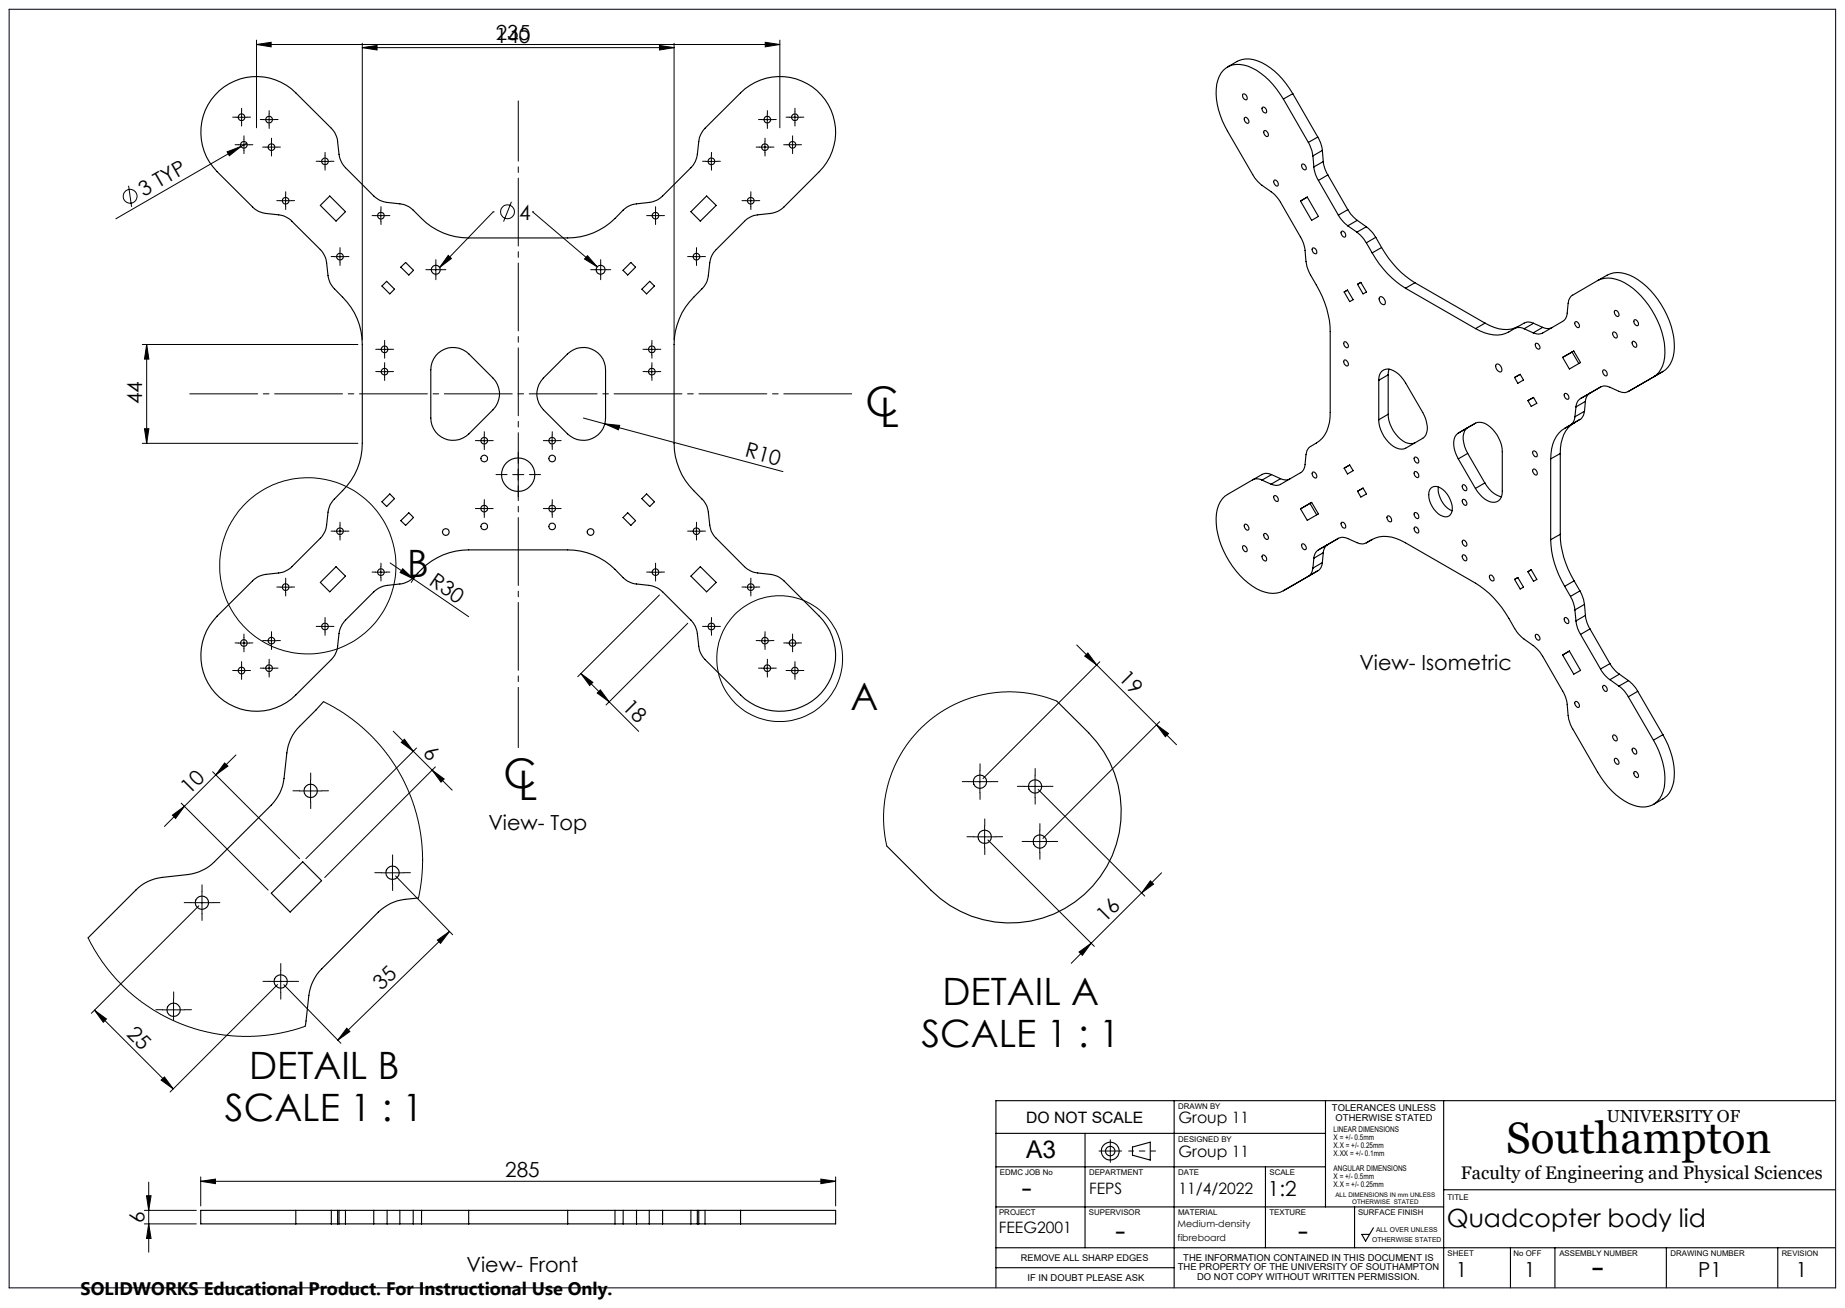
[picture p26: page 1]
3 TYP 44; View- Isometric; View- Front; DETAIL A SCALE 1 : 1; DETAIL B; SCALE 1 : 1; Group 11; fibreboard FEEG2001; Quadcopter body lid; - FEPS - -; View- Top; 1 SHEET; No OFF; ASSEMBLY NUMBER; DRAWING NUMBER; REVISION; PROJECT; SUPERVISOR; MATERIAL; TEXTURE; SURFACE FINISH; TOLERANCES UNLESS OTHERWISE STATED; DRAWN BY; DESIGNED BY; EDMC JOB No; DEPARTMENT; DATE; SCALE; DO NOT SCALE; LINEAR DIMENSIONS X = +/- 0.5mm X.X = +/- 0.25mm X.XX = +/- 0.1mm ANGULAR DIMENSIONS X = +/- 0.5mm

Southampton UNIVERSITY OF

Faculty of Engineering and Physical Sciences

ALL DIMENSIONS IN mm UNLESS
OTHERWISE STATED

ALL OVER UNLESS

REMOVE ALL SHARP EDGES
IF IN DOUBT PLEASE ASK

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

SOLIDWORKS Educational Product. For Instructional Use Only.

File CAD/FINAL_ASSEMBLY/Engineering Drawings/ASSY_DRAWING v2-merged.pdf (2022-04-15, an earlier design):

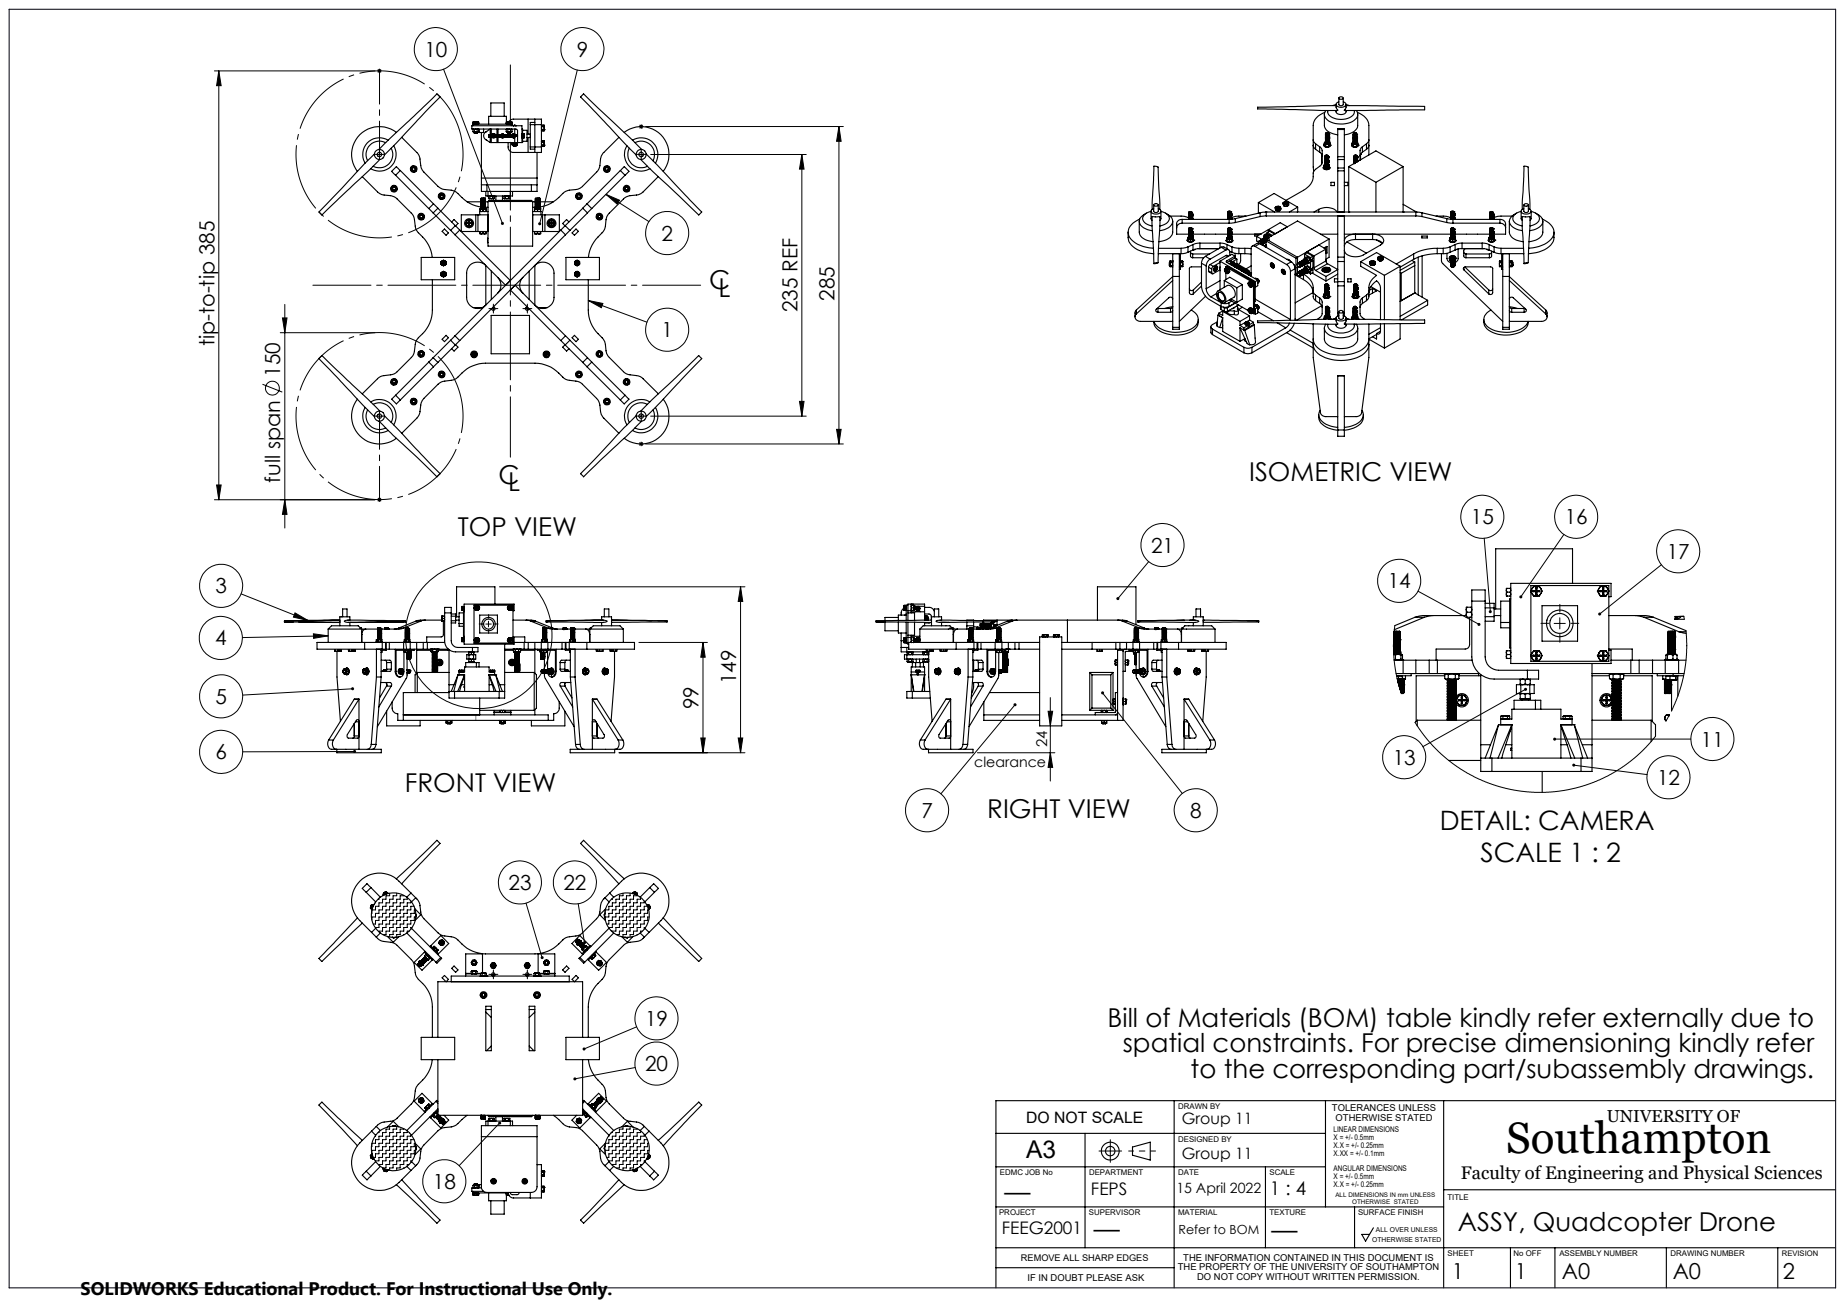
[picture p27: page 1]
235 REF; full span 150; TOP VIEW; FRONT VIEW; RIGHT VIEW; ISOMETRIC VIEW; DETAIL: CAMERA SCALE 1 : 2; FEPS; 15 April 2022; Group 11; SHEET; No OFF; ASSEMBLY NUMBER; DRAWING NUMBER; REVISION; PROJECT; SUPERVISOR; MATERIAL; TEXTURE; SURFACE FINISH; TOLERANCES UNLESS OTHERWISE STATED; DRAWN BY; DESIGNED BY; EDMC JOB No; DEPARTMENT; DATE; SCALE; DO NOT SCALE; LINEAR DIMENSIONS X = +/- 0.5mm X.X = +/- 0.25mm X.XX = +/- 0.1mm ANGULAR DIMENSIONS X = +/- 0.5mm

tip-to-tip 385

Bill of Materials (BOM) table kindly refer externally due to
spatial constraints. For precise dimensioning kindly refer
to the corresponding part/subassembly drawings.

Southampton UNIVERSITY OF

Faculty of Engineering and Physical Sciences
ASSY, Quadcopter Drone

ALL DIMENSIONS IN mm UNLESS
OTHERWISE STATED

Refer to BOM

ALL OVER UNLESS

REMOVE ALL SHARP EDGES
IF IN DOUBT PLEASE ASK

THE INFORMATION CONTAINED IN THIS DOCUMENT IS
THE PROPERTY OF THE UNIVERSITY OF SOUTHAMPTON
DO NOT COPY WITHOUT WRITTEN PERMISSION.

SOLIDWORKS Educational Product. For Instructional Use Only.

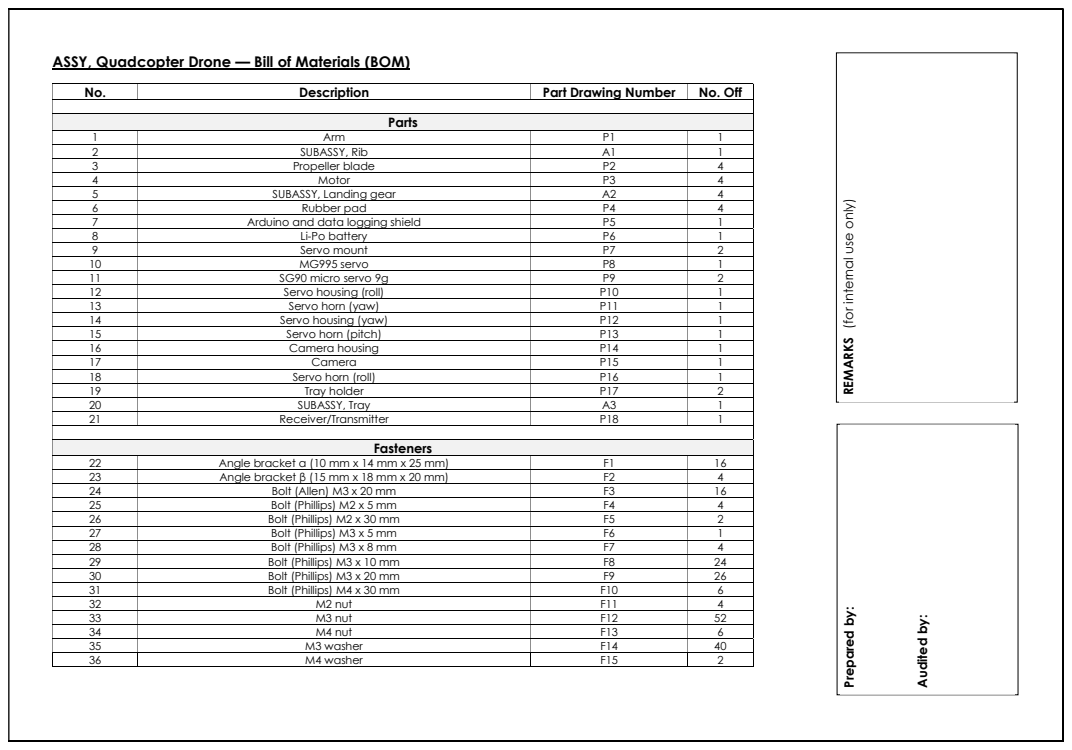
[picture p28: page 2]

ASSY, Quadcopter Drone — Bill of Materials (BOM)

1 | Arm | P1 | 1
2 | SUBASSY, Rib | A1 | 1
3 | Propeller blade | P2 | 4
4 | Motor | P3 | 4
5 | SUBASSY, Landing gear | A2 | 4
6 | Rubber pad | P4 | 4
7 | Arduino and data logging shield | P5 | 1
8 | Li-Po battery | P6 | 1
9 | Servo mount | P7 | 2
10 | MG995 servo | P8 | 1
11 | SG90 micro servo 9g | P9 | 2
12 | Servo housing (roll) | P10 | 1
13 | Servo horn (yaw) | P11 | 1
14 | Servo housing (yaw) | P12 | 1
15 | Servo horn (pitch) | P13 | 1
16 | Camera housing | P14 | 1
17 | Camera | P15 | 1
18 | Servo horn (roll) | P16 | 1
19 | Tray holder | P17 | 2
20 | SUBASSY, Tray | A3 | 1
21 | Receiver/Transmitter | P18 | 1

22 | Angle bracket α (10 mm x 14 mm x 25 mm) | F1 | 16
23 | Angle bracket β (15 mm x 18 mm x 20 mm) | F2 | 4
24 | Bolt (Allen) M3 x 20 mm | F3 | 16
25 | Bolt (Phillips) M2 x 5 mm | F4 | 4
26 | Bolt (Phillips) M2 x 30 mm | F5 | 2
27 | Bolt (Phillips) M3 x 5 mm | F6 | 1
28 | Bolt (Phillips) M3 x 8 mm | F7 | 4
29 | Bolt (Phillips) M3 x 10 mm | F8 | 24
30 | Bolt (Phillips) M3 x 20 mm | F9 | 26
31 | Bolt (Phillips) M4 x 30 mm | F10 | 6
32 | M2 nut | F11 | 4
33 | M3 nut | F12 | 52
34 | M4 nut | F13 | 6
35 | M3 washer | F14 | 40

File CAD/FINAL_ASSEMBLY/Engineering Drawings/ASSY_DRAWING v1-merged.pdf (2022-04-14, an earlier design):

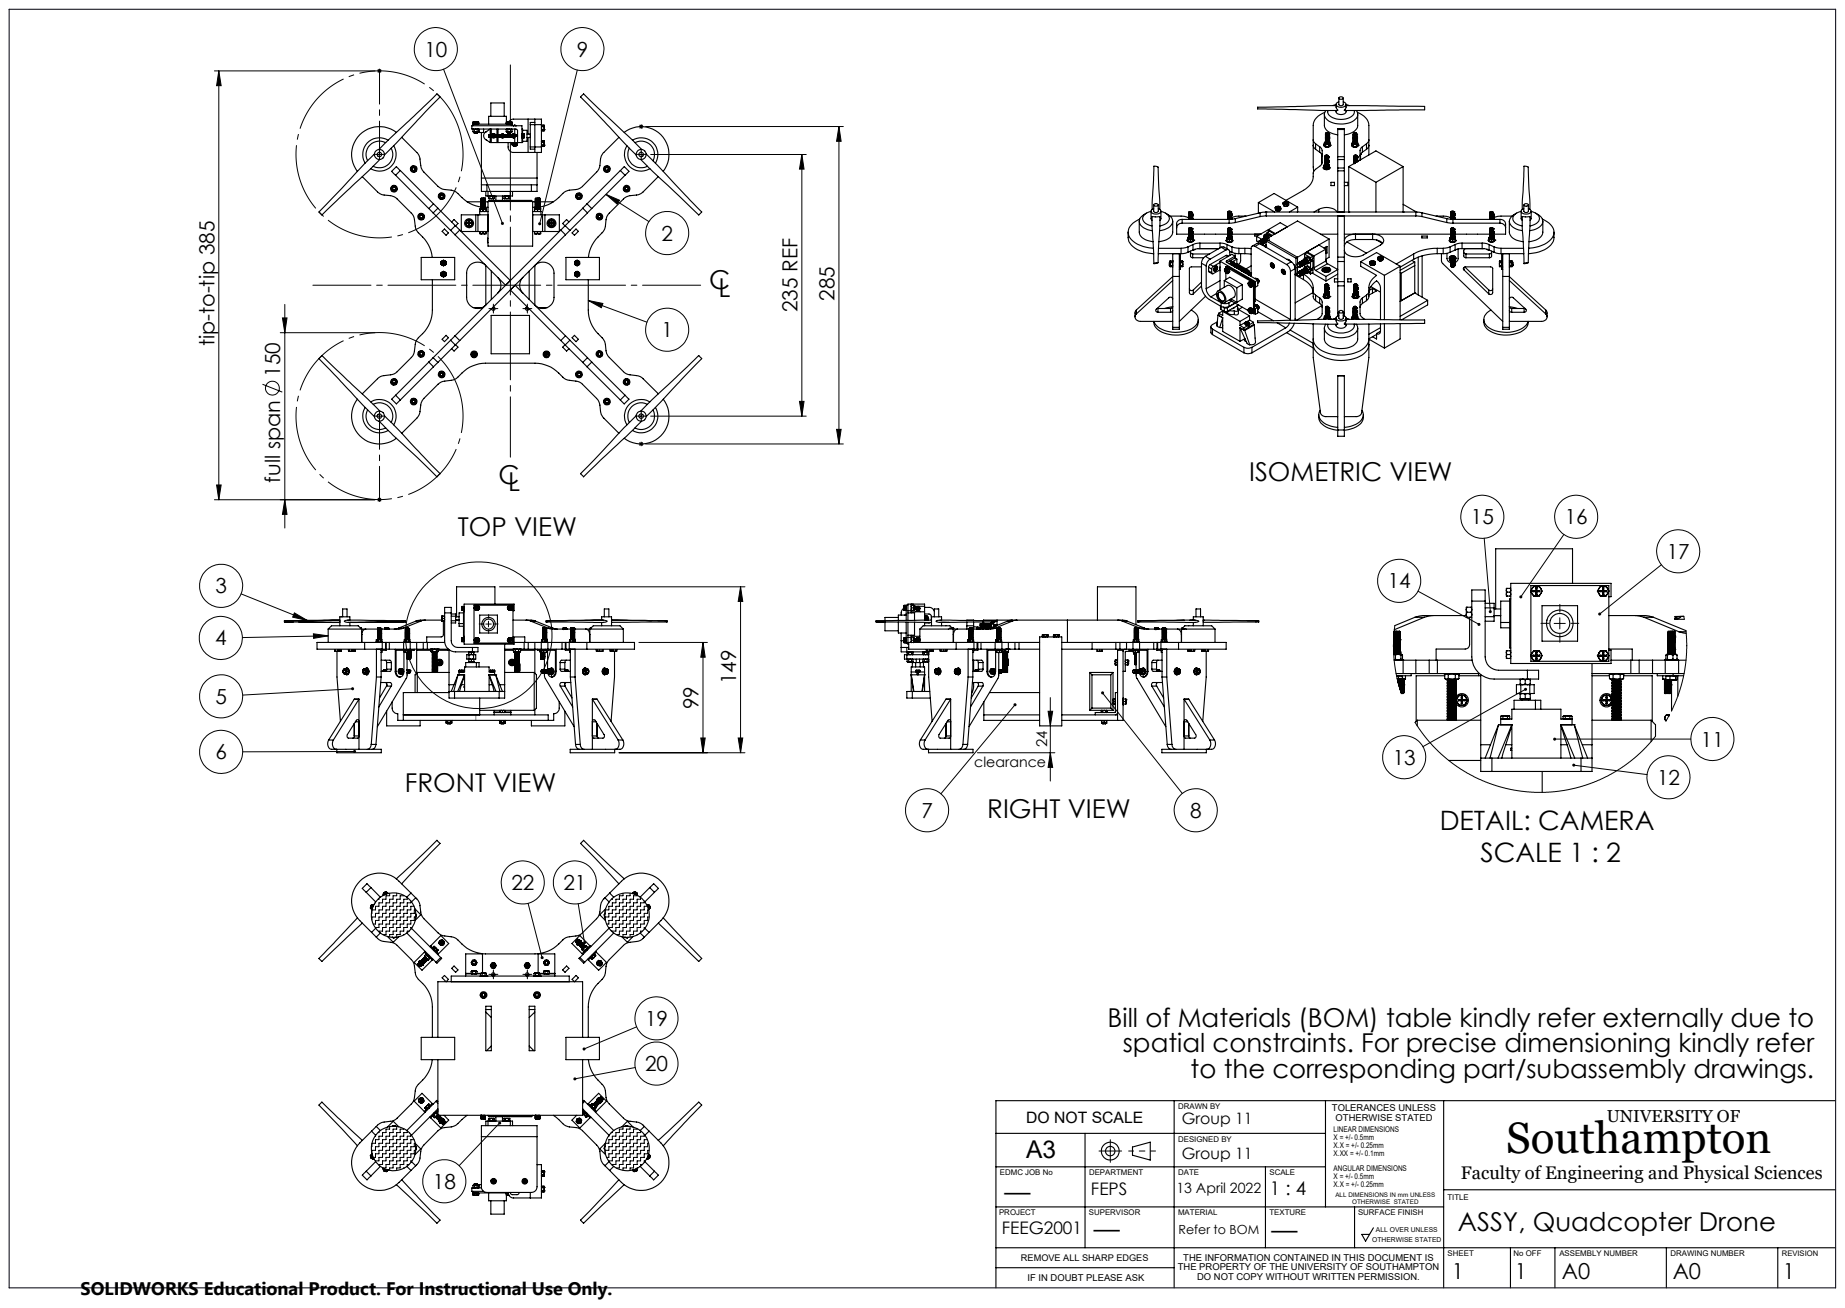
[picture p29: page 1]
235 REF; full span 150; TOP VIEW; FRONT VIEW; RIGHT VIEW; ISOMETRIC VIEW; DETAIL: CAMERA SCALE 1 : 2; FEPS; 13 April 2022; Group 11; SHEET; No OFF; ASSEMBLY NUMBER; DRAWING NUMBER; REVISION; PROJECT; SUPERVISOR; MATERIAL; TEXTURE; SURFACE FINISH; TOLERANCES UNLESS OTHERWISE STATED; DRAWN BY; DESIGNED BY; EDMC JOB No; DEPARTMENT; DATE; SCALE; DO NOT SCALE; LINEAR DIMENSIONS X = +/- 0.5mm X.X = +/- 0.25mm X.XX = +/- 0.1mm ANGULAR DIMENSIONS X = +/- 0.5mm

tip-to-tip 385

Bill of Materials (BOM) table kindly refer externally due to
spatial constraints. For precise dimensioning kindly refer
to the corresponding part/subassembly drawings.

Southampton UNIVERSITY OF

Faculty of Engineering and Physical Sciences
ASSY, Quadcopter Drone

ALL DIMENSIONS IN mm UNLESS
OTHERWISE STATED

Refer to BOM

ALL OVER UNLESS

REMOVE ALL SHARP EDGES
IF IN DOUBT PLEASE ASK

THE INFORMATION CONTAINED IN THIS DOCUMENT IS
THE PROPERTY OF THE UNIVERSITY OF SOUTHAMPTON
DO NOT COPY WITHOUT WRITTEN PERMISSION.

SOLIDWORKS Educational Product. For Instructional Use Only.

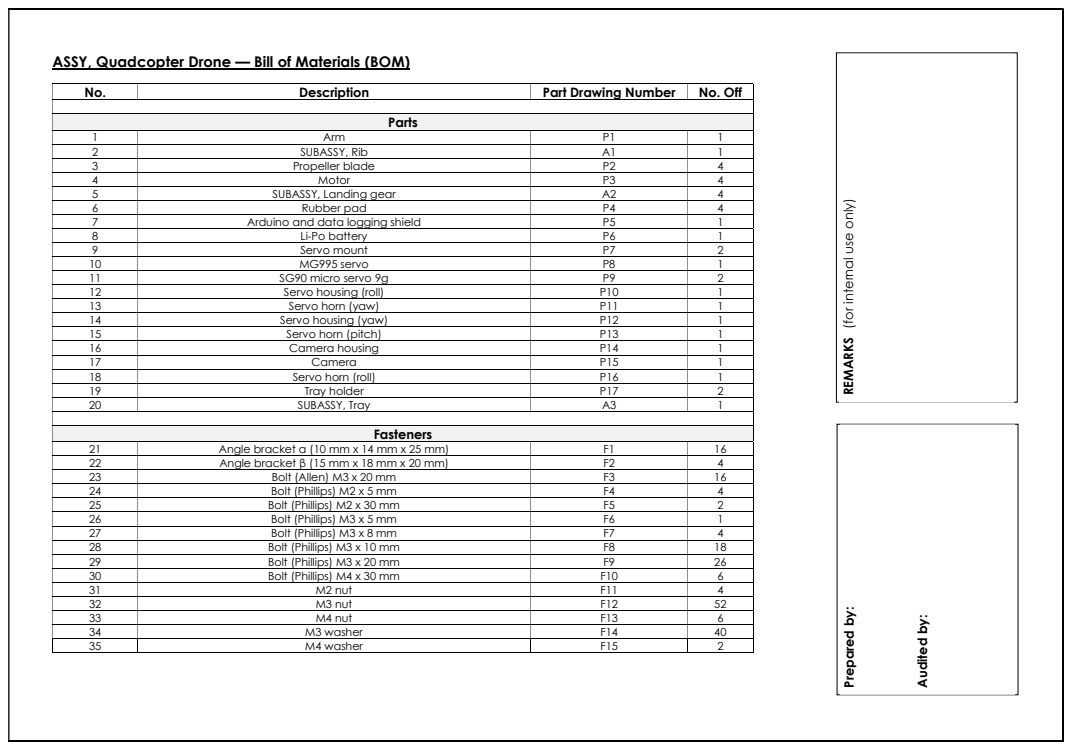
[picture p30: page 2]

ASSY, Quadcopter Drone — Bill of Materials (BOM)

1 | Arm | P1 | 1
2 | SUBASSY, Rib | A1 | 1
3 | Propeller blade | P2 | 4
4 | Motor | P3 | 4
5 | SUBASSY, Landing gear | A2 | 4
6 | Rubber pad | P4 | 4
7 | Arduino and data logging shield | P5 | 1
8 | Li-Po battery | P6 | 1
9 | Servo mount | P7 | 2
10 | MG995 servo | P8 | 1
11 | SG90 micro servo 9g | P9 | 2
12 | Servo housing (roll) | P10 | 1
13 | Servo horn (yaw) | P11 | 1
14 | Servo housing (yaw) | P12 | 1
15 | Servo horn (pitch) | P13 | 1
16 | Camera housing | P14 | 1
17 | Camera | P15 | 1
18 | Servo horn (roll) | P16 | 1
19 | Tray holder | P17 | 2
20 | SUBASSY, Tray | A3 | 1

21 | Angle bracket α (10 mm x 14 mm x 25 mm) | F1 | 16
22 | Angle bracket β (15 mm x 18 mm x 20 mm) | F2 | 4
23 | Bolt (Allen) M3 x 20 mm | F3 | 16
24 | Bolt (Phillips) M2 x 5 mm | F4 | 4
25 | Bolt (Phillips) M2 x 30 mm | F5 | 2
26 | Bolt (Phillips) M3 x 5 mm | F6 | 1
27 | Bolt (Phillips) M3 x 8 mm | F7 | 4
28 | Bolt (Phillips) M3 x 10 mm | F8 | 18
29 | Bolt (Phillips) M3 x 20 mm | F9 | 26
30 | Bolt (Phillips) M4 x 30 mm | F10 | 6
31 | M2 nut | F11 | 4
32 | M3 nut | F12 | 52
33 | M4 nut | F13 | 6
34 | M3 washer | F14 | 40

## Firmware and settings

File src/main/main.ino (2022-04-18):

/* ===  FEEG2001 Group 11: Combined Gimbal and Logging Firmware  ===
 *
 * Pin  No.   |            Description          |
 * ==============================================
 * Pin  02    |   MPU Interrupt Pin             |
 * Pin  03    |   Toggle Pin                    |
 * Pin  08    |   Roll Servo                    |
 * Pin  09    |   Pitch Servo                   |
 * Pin  10    |   DataLogger Shield ChipSelect  |
 * Pin  11    |   Yaw Servo                     |
 * Pin  12    |   DMP Initialisation Status     |
 * Pin  13    |   MPU Status                    |
 * Pin  A4    |   MPU SDA                       |
 * Pin  A5    |   MPU SCL                       |
 */

// === Watchdog timer handling ===
#include <avr/wdt.h>

// === MPU required libraries ===
#include "I2Cdev.h"
#include "MPU6050_6Axis_MotionApps20.h"
#if I2CDEV_IMPLEMENTATION == I2CDEV_ARDUINO_WIRE
    #include <Wire.h>
#endif

// === Data logger required libraries ===
#include <SD.h>
#include <Wire.h>
#include "RTClib.h"

// === Gimbal required libraries ===
#include <Servo.h>

// === MPU initialisation ===
MPU6050 mpu (0x69);
#define OUTPUT_READABLE_YAWPITCHROLL      // to see the yaw/pitch/roll angles (in degrees) calculated from the quaternions coming from the FIFO.
#define INTERRUPT_PIN 2                   // use pin 2 on Arduino Uno & most boards
#define LED_PIN 13                        // MPU status now tied to Pin 13 LED
bool blinkState = false;

// === MPU control/status variables ===
bool dmpReady = false;                    // set true if DMP init was successful
uint8_t mpuIntStatus;                     // holds actual interrupt status byte from MPU
uint8_t devStatus;                        // return status after each device operation (0 = success, !0 = error)
uint16_t packetSize;                      // expected DMP packet size (default is 42 bytes)
uint16_t fifoCount;                       // count of all bytes currently in FIFO
uint8_t fifoBuffer[64];                   // FIFO storage buffer

// === Orientation/motion variables ===
Quaternion q;                             // [w, x, y, z]         quaternion container
VectorInt16 aa;                           // [x, y, z]            accel sensor measurements
VectorInt16 aaReal;                       // [x, y, z]            gravity-free accel sensor measurements
VectorInt16 aaWorld;                      // [x, y, z]            world-frame accel sensor measurements
VectorFloat gravity;                      // [x, y, z]            gravity vector
float euler[3];                           // [psi, theta, phi]    Euler angle container
float ypr[3];                             // [yaw, pitch, roll]   yaw/pitch/roll container and gravity vector

// === Interrupt detection routine ===
volatile bool mpuInterrupt = false;       // indicates whether MPU interrupt pin has gone high
void dmpDataReady() {
    mpuInterrupt = true;
}

// === DataLogger Initialisation ===
#define LOG_INTERVAL 1000
#define SYNC_INTERVAL 1000 // mills between calls to flush() - to write data to the card
uint32_t syncTime = 0; // time of last sync()

#define ECHO_TO_SERIAL   0 // echo data to serial port
#define WAIT_TO_START    0 // Wait for serial input in setup()
RTC_DS1307 RTC; // define the Real Time Clock object

// For the data logging shield, use digital pin 10 for the SD cs line
const int chipSelect = 10;

// Logging file object
File logfile;

// Exception handling
void error(char *str) {
    Serial.print("error: ");
    Serial.println(str);
    while(1);
}

// === Servo Initialisation ===
Servo servo_y, servo_p, servo_r;

// === Toggle Initialisation ===
volatile bool lock_flag;
volatile int pwm_value = 0;
volatile int prev_time = 0;

void rising() {
    attachInterrupt(1, falling, FALLING);
    prev_time = micros();
}
 
void falling() {
    attachInterrupt(1, rising, RISING);
    pwm_value = micros() - prev_time;
    // Serial.println(pwm_value);
    if (pwm_value < 1200){
        lock_flag = true;
    }
    else if (pwm_value > 1800){
        lock_flag = false;
    }
}


void setup() {
// === Serial Setup ===
    Serial.begin(115200);  // Change to project baud rate
    // Serial.print(F("Current date: "));
    // Serial.println(__DATE__);
    // Serial.print(F("Current time: "));
    // Serial.println(__TIME__);
  
// === MPU Setup ===
    // Join I2C bus
    #if I2CDEV_IMPLEMENTATION == I2CDEV_ARDUINO_WIRE
        Wire.begin();
        Wire.setClock(250000);
    #elif I2CDEV_IMPLEMENTATION == I2CDEV_BUILTIN_FASTWIRE
        Fastwire::setup(400, true);
    #endif

// === Initialise MPU device ===
    // Serial.println(F("Initialising I2C devices..."));
    mpu.initialize();
    pinMode(INTERRUPT_PIN, INPUT);

// === Verify connection ===
    // Serial.println(F("Testing device connections..."));
    Serial.println(mpu.testConnection() ? F("MPU6050 connection successful") : F("MPU6050 connection failed"));

// === Load and configure DMP ===
    //Serial.println(F("Initializing DMP..."));
    devStatus = mpu.dmpInitialize();

// === GYRO OFFSET HERE! ===
    mpu.setXGyroOffset(17);
    mpu.setYGyroOffset(-69);
    mpu.setZGyroOffset(27);
    mpu.setZAccelOffset(1551);
  
// === Verify MPU setup ===
    if (devStatus == 0) {
        // Calibration Time: generate offsets and calibrate our MPU6050
        // mpu.CalibrateAccel(6);
        // mpu.CalibrateGyro(6);
        // mpu.PrintActiveOffsets();
    
        // Turn on the DMP, now that it's ready
        // Serial.println(F("Enabling DMP..."));
        mpu.setDMPEnabled(true);

        // Enable Arduino interrupt detection
        // Serial.print(F("Enabling interrupt detection (Arduino external interrupt "));
        // Serial.print(digitalPinToInterrupt(INTERRUPT_PIN));
        // Serial.println(F(")..."));
        attachInterrupt(digitalPinToInterrupt(INTERRUPT_PIN), dmpDataReady, RISING);
        mpuIntStatus = mpu.getIntStatus();

        // Set our DMP Ready flag so the main loop() function knows it's okay to use it
        // Serial.println(F("DMP ready! Waiting for first interrupt..."));
        dmpReady = true;

        // Get expected DMP packet size for later comparison
        packetSize = mpu.dmpGetFIFOPacketSize();
    } else {
        // ERROR!
        // 1 = initial memory load failed
        // 2 = DMP configuration updates failed
        // (if it's going to break, usually the code will be 1)
        // Serial.print(F("DMP Initialization failed (code "));
        // Serial.print(devStatus);
        // Serial.println(F(")."));
    } 

// === Configure LED for output ===
    pinMode(LED_PIN, OUTPUT);

// === DataLogger Setup ===

    // Initialise the SD card
    //  Serial.println(F("Initialising SD card..."));  // make sure that the default chip select pin is set to output, even if you don't use it:
    pinMode(10, OUTPUT);


    // See if the card is present and can be initialised:
    if (!SD.begin(chipSelect)) {
        error("Card failed, or not present");
    }
    Serial.println("card initialized.");
  
    // Create a new file
    char filename[] = "LOGGER00.CSV";
    for (uint8_t i = 0; i < 100; i++) {
        filename[6] = i/10 + '0';  // ASCII
        filename[7] = i%10 + '0';
        if (!SD.exists(filename)) {
            // only open a new file if it doesn't exist
            logfile = SD.open(filename, FILE_WRITE); 
            break;  // leave the loop
        }
    }
    if (!logfile) {
        error("couldn't create file");
    }

    Wire.begin();  
    if (!RTC.begin()) {
        logfile.println("RTC failed");
    }

    // Serial.print(F("Logging to: "));
    // Serial.println(filename);

// === Servo Set Up ===
    servo_y.attach(11);
    servo_p.attach(9);
    servo_r.attach(8);

// === Toggle Set Up ===
    attachInterrupt(1, rising, RISING);
    wdt_enable(WDTO_2S);  // if the watchdog is not called within 2 seconds, the microcontroller reboots
}


void loop() {
// === MPU Main Loop ===
    // If programming failed, don't try to do anything
    if (!dmpReady) return;
    // Read a packet from FIFO
    // Wait for MPU interrupt or extra packet(s) available
    while (!mpuInterrupt && fifoCount < packetSize) {
        if (mpuInterrupt && fifoCount < packetSize) {                     // try to get out of the infinite loop 
            fifoCount = mpu.getFIFOCount();
        }                                                                 //if you are really paranoid you can frequently test in between other stuff to see if mpuInterrupt is true, and if so, "break;" from the while() loop to immediately process the MPU data
    }

    // Reset interrupt flag and get INT_STATUS byte
    mpuInterrupt = false;
    mpuIntStatus = mpu.getIntStatus();

    // Get current FIFO count
    fifoCount = mpu.getFIFOCount();

    // Check for overflow
    if ((mpuIntStatus & _BV(MPU6050_INTERRUPT_FIFO_OFLOW_BIT)) || fifoCount >= 1024) {
        mpu.resetFIFO();
        fifoCount = mpu.getFIFOCount();
        // Serial.println(F("FIFO overflow!"));
    } else if (mpuIntStatus & _BV(MPU6050_INTERRUPT_DMP_INT_BIT)) { 
        mpu.getFIFOBytes(fifoBuffer, packetSize);
        fifoCount -= packetSize;

#ifdef OUTPUT_READABLE_YAWPITCHROLL // Display Euler angles in degrees
        mpu.dmpGetQuaternion(&q, fifoBuffer);
        mpu.dmpGetGravity(&gravity, &q);
        mpu.dmpGetYawPitchRoll(ypr, &q, &gravity);
        mpu.dmpGetLinearAccel(&aaReal, &aa, &gravity);
        

// === Gimbal Implementation ===
        // Lock gimbal if toggle is high
        if (lock_flag) {
            servo_y.write(90);
            servo_p.write(90);
            servo_r.write(90);
            Serial.println(lock_flag);
        } else {  // Else continue with gimbal operation
            ypr[0] *= 180 / M_PI;
            ypr[1] *= 180 / M_PI;
            ypr[2] *= 180 / M_PI;
            uint8_t servo0Value = map(ypr[0], -90, 90, 0, 180);
            uint8_t servo1Value = map(ypr[1], -90, 90, 0, 180);
            uint8_t servo2Value = map(ypr[2], -90, 90, 180, 0);
            Serial.println(lock_flag);
              
            // Control the servos according to the MPU6050 orientation
            servo_y.write(servo0Value);
            servo_p.write(servo1Value);
            servo_r.write(servo2Value); 
        }
    }
#endif  // OUTPUT_READABLE_YAWPITCHROLL
    uint32_t m = millis();
    float dataArray[7] = {m, ypr[0], ypr[1], ypr[2], aaReal.x, aaReal.y, aaReal.z};
    String logString = "";

    for (uint8_t i = 0; i < 7; i++) {
        logString += String(dataArray[i]);
        if (i < 6) {
            logString += ",";
        }
    }
    Serial.println(logString);
    if ((millis() - syncTime) < SYNC_INTERVAL) return;
    syncTime = millis();
    logfile.println(String(logString));
    logfile.flush();
    wdt_reset();  // call the watchdog
}

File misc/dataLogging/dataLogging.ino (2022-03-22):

/* ============================================
I2Cdev device library code is placed under the MIT License
Copyright (c) 2012 Jeff Rowberg

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
THE SOFTWARE IS PROVIDED "AS IS", WITHOUT WARRANTY OF ANY KIND, EXPRESS OR
IMPLIED, INCLUDING BUT NOT LIMITED TO THE WARRANTIES OF MERCHANTABILITY,
FITNESS FOR A PARTICULAR PURPOSE AND NONINFRINGEMENT. IN NO EVENT SHALL THE
AUTHORS OR COPYRIGHT HOLDERS BE LIABLE FOR ANY CLAIM, DAMAGES OR OTHER
LIABILITY, WHETHER IN AN ACTION OF CONTRACT, TORT OR OTHERWISE, ARISING FROM,
OUT OF OR IN CONNECTION WITH THE SOFTWARE OR THE USE OR OTHER DEALINGS IN
THE SOFTWARE.
============================================ */

#pragma once
#include <SD.h>
#include <Wire.h>
#include "RTClib.h"
#include "I2Cdev.h"
#if I2CDEV_IMPLEMENTATION == I2CDEV_ARDUINO_WIRE
    #include "Wire.h"
#endif
#include "MPU6050_6Axis_MotionApps20.h"

// For debug use
#define DEBUG {\
    Serial.print("\nDEBUG: LINE ");\
    Serial.println(__LINE__);\
}

// Print error to serial monitor
#define cerr(x) {\
    Serial.print("ERROR: ");\
    Serial.println(x);\
    Serial.println("Please reset/restart the program.");\
    while(true);\
}

// MPU6050 mpu;
MPU6050 mpu(0x69);
File logfile;

#define INTERRUPT_PIN 2  // use pin 2 on Arduino Uno
bool blinkState = false;

// MPU control/status variables
bool dmpReady = false;
uint8_t mpuIntStatus;
uint8_t devStatus;
uint16_t packetSize;
uint16_t fifoCount;
uint8_t fifoBuffer[64];

// Orientation/motion variables
Quaternion q;           // [w, x, y, z]         quaternion container
VectorInt16 aa;         // [x, y, z]            accel sensor measurements
VectorInt16 aaReal;     // [x, y, z]            gravity-free accel sensor measurements
VectorInt16 aaWorld;    // [x, y, z]            world-frame accel sensor measurements
VectorFloat gravity;    // [x, y, z]            gravity vector
float euler[3];         // [psi, theta, phi]    Euler angle container
float ypr[3];           // [yaw, pitch, roll]   yaw/pitch/roll container and gravity vector

// how many milliseconds between grabbing data and logging it
//#define LOG_INTERVAL 1000 // how many milliseconds between grabbing data and logging it. mills between entries (reduce to take more/faster data)
//#define SYNC_INTERVAL 1000  // mills between calls to flush() - to write data to the card
//uint32_t syncTime = 0;  // time of last sync()
uint32_t logMillis = millis();
#define ECHO_TO_SERIAL  // Echo data to serial port
const int chipSelect = 10;  // for the data logging shield, use digital pin 10

// Interrupt detection routine
volatile bool mpuInterrupt = false;  // Indicates whether MPU interrupt pin has gone high
void dmpDataReady() {
    mpuInterrupt = true;
}

// =======================================================================================================

void setup() {
    // Join I2C bus (I2Cdev library doesn't do this automatically)
#if I2CDEV_IMPLEMENTATION == I2CDEV_ARDUINO_WIRE
    Wire.begin();
    Wire.setClock(400000);  // 400kHz I2C clock. Comment this line if having compilation difficulties
#elif I2CDEV_IMPLEMENTATION == I2CDEV_BUILTIN_FASTWIRE
    Fastwire::setup(400, true);
#endif

    // 115200 baud is chosen because it is required for Teapot Demo output, but it
    // depends on your project.
    Serial.begin(38400);
    delay(1000);  // crucial for stability

    Serial.println("Send any character to start >>>");
    while (!Serial.available());

    // Initialise device
    Serial.println(F("Initialising I2C devices..."));
    mpu.initialize();
    pinMode(INTERRUPT_PIN, INPUT);

    // Verify connection
    Serial.println(F("Testing device connections..."));
    Serial.println(mpu.testConnection() ? F("MPU6050 connection successful.") : F("MPU6050 connection failed."));

    // Load and configure the DMP
    Serial.println(F("Initialising DMP..."));
    devStatus = mpu.dmpInitialize();

    // !!!! IMPORTANT !!!!
    // Supply your own gyro offset values here, scaled for min sensitivity
    mpu.setXGyroOffset(220);
    mpu.setYGyroOffset(76);
    mpu.setZGyroOffset(-85);
    mpu.setZAccelOffset(1788); // 1688 factory default for my test chip

    // Make sure it worked (returns 0 if so)
    if (devStatus == 0) {
        Serial.println(F("Enabling DMP..."));
        mpu.setDMPEnabled(true);

        // Enable Arduino interrupt detection
        Serial.print(F("Enabling interrupt detection (Arduino external interrupt "));
        Serial.print(digitalPinToInterrupt(INTERRUPT_PIN));
        Serial.println(F(")..."));
        attachInterrupt(digitalPinToInterrupt(INTERRUPT_PIN), dmpDataReady, RISING);
        mpuIntStatus = mpu.getIntStatus();

        // Set our DMP Ready flag so the main loop() function knows it's okay to use it
        Serial.println(F("DMP ready! Waiting for first interrupt..."));
        dmpReady = true;

        // get expected DMP packet size for later comparison
        packetSize = mpu.dmpGetFIFOPacketSize();
    } else {
        // Error values:
        // 1 = Initial memory load failed
        // 2 = DMP configuration updates failed
        // (if it's going to break, usually the code will be 1)
        Serial.print(F("DMP initialisation failed (code "));
        Serial.print(devStatus);
        Serial.println(F(")."));
    }

    // Configure LED for output
    pinMode(LED_BUILTIN, OUTPUT);

    // Initialise the SD card
    Serial.println("Initialising SD card...");
    // make sure that the default chip select pin is set to
    // output, even if you don't use it:
    pinMode(10, OUTPUT);

    // See if the card is present and can be initialised
    if (!SD.begin(chipSelect)) {
        cerr("Card failed or not present.");
    }
    Serial.println("Card initialised.");

    // Create a new file
    char filename[] = "LOGGER00.CSV";
    for (int i = 0; i < 100; i++) {
        filename[6] = i/10 + '0';
        filename[7] = i%10 + '0';
        // only open a new file if it doesn't exist
        if (!SD.exists(filename)) {
            logfile = SD.open(filename, FILE_WRITE);
            break;  // leave the loop
        }
    }

    if (!logfile) {
        cerr("Couldn't create file.");
    }

    Serial.print("Logging to: ");
    Serial.println(filename);
    logfile.println("Program runtime (s), Yaw, Pitch, Roll");
}

// =======================================================================================================
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

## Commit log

2022-02-12 Add 3D CAD files via upload
    26 items total
    [Assembly1.SLDASM, Assembly2.SLDASM, arm.SLDPRT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]
2022-02-12 Add current development and changelog
2022-03-01 rename SolidWorks CAD folder to SolidWorks_CAD
    [Assembly1.SLDASM, Assembly2.SLDASM, angle_bracket_15x15x10.SLDPRT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]
2022-04-07 Updated to current progress
2022-04-07 re-organised cad
    [Assembly1.SLDASM, Assembly2.SLDASM, angle_bracket_15x15x10.SLDPRT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]
2022-04-07 re-organising cd
    [Assembly1.SLDASM, Assembly2.SLDASM, angle_bracket_15x15x10.SLDPRT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]
2022-04-07 re-organising CAD
    [BODYLID6_MDF_1PCS_FINAL.DXF, LDGFEM_S_MDF_4PCS.DXF, LDGMALE_S_MDF_4PCS.DXF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]
2022-04-08 upload CAD files (2021-22 version)
    [ASSY.SLDASM, LDG_GEAR_E_FEM_2.SLDPRT, LDG_GEAR_E_mal_2.SLDPRT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]
2022-04-10 Gimbal code written, not tested. FIFO issue needs resolving.
    [DIY_Arduino_Gimbal_Code_-_Based_on__MPU6050_DMP6_Example.ino, main.ino]
2022-04-11 optimise directory
    [camera_housing_new.SLDPRT, rear_tray_holder.SLDPRT, servohousing1.SLDPRT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]
2022-04-11 optimise code
    float servo0Value = map(ypr[0], -90, 90, 0, 180);
    float servo1Value = map(ypr[1], -90, 90, 0, 180);
    float servo2Value = map(ypr[2], -90, 90, 180, 0);
    are equivalent to:
    float servo0Value = ypr[0] + 90;
    float servo1Value = ypr[1] + 90;
    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
2022-04-12 update final assembly CAD
    [L_bracket_alpha.SLDPRT, L_bracket_beta.SLDPRT, SUBASSY_tray.SLDASM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]
2022-04-12 update assembly CAD files
    [LDG_GEAR_E_mal_2.SLDPRT, body_lid5.SLDPRT, bolt_phillips_M3_5mm.SLDPRT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]
2022-04-14 complete final assembly CAD files
    [SUBASSY_tray.SLDASM, arduino_uno.SLDPRT, battery.SLDPRT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]
2022-04-14 Fixed FIFO Overflow and misc. bugs
    Need to add flush/refresh function for SD card reader.
    Need to solve jittering issue.
    [main.ino, toggletest.ino]
2022-04-15 new BOM, drawing and video
    [SUBASSY_landinggear.SLDDRW]
2022-04-15 Stability Fix, Data Logging Still Buggy
    Use rollback if problematic
    [rollback_15042022.ino]
2022-04-16 Added watchdog function
    That reboots the arduino if it hangs
    [main.ino]
2022-04-16 add drawing files
    [SUBASSY_tray.SLDDRW]
2022-04-16 update assembly gimbal and battery placement
    [body_lid5.SLDPRT, servo_horn_round.SLDPRT]
2022-04-18 add assembly drawings v3
    [SUBASSY_landinggear.SLDDRW, body_lid5.SLDPRT, tx_rx.SLDPRT]
2022-04-18 Updated FDR
    [18_04_2021_FDR.csv, LOGGER00.CSV, LOGGER01.CSV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]
2022-04-18 add FEA analyses
    [SUBASSY_body_lid5_with_ribs.IGS, SUBASSY_landinggear.IGS, body_lid5.SLDPRT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]
